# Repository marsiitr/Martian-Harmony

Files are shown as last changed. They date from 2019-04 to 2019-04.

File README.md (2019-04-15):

# Martian-Harmony
## Srishti 2019 
The idea was to build a robot that can play musical instruments in the same fashion as humans. It consists of various instruments like Flute, Keyboard, Guitar, etc. All these instruments are being played using different mechanisms.
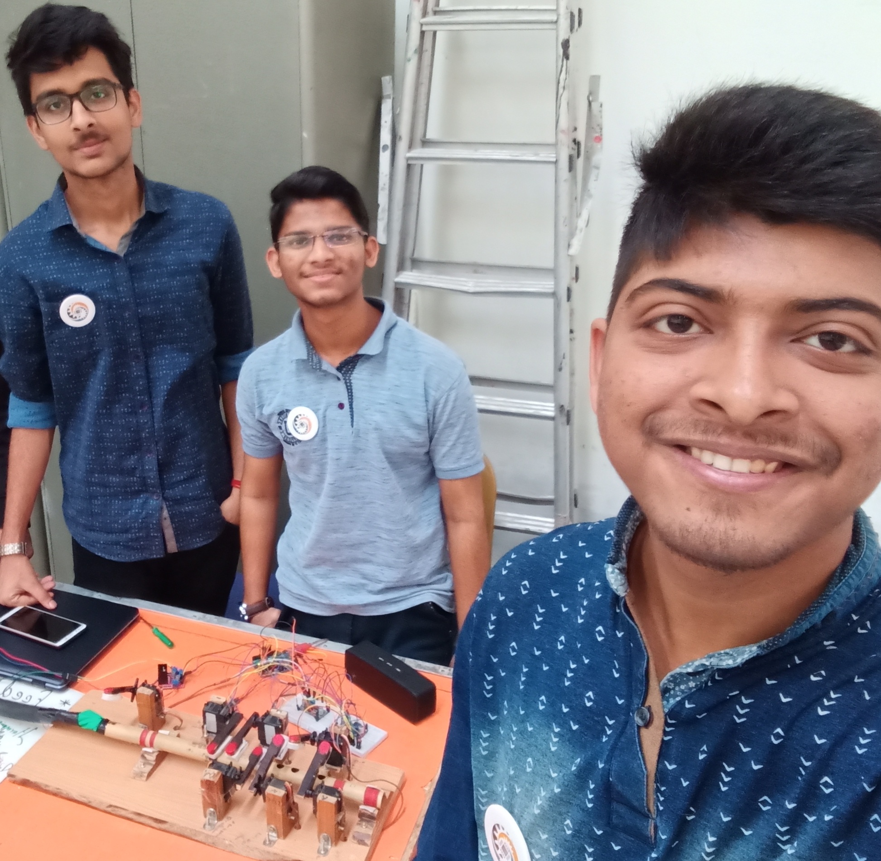
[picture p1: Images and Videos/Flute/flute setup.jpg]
Flute playing bot


To read about the working of Flute Playing Bot, click [here.](https://github.com/visvash/Martian-Harmony/blob/master/Src/Flute/README.md "Martian-Harmony Flute Playing Bot")

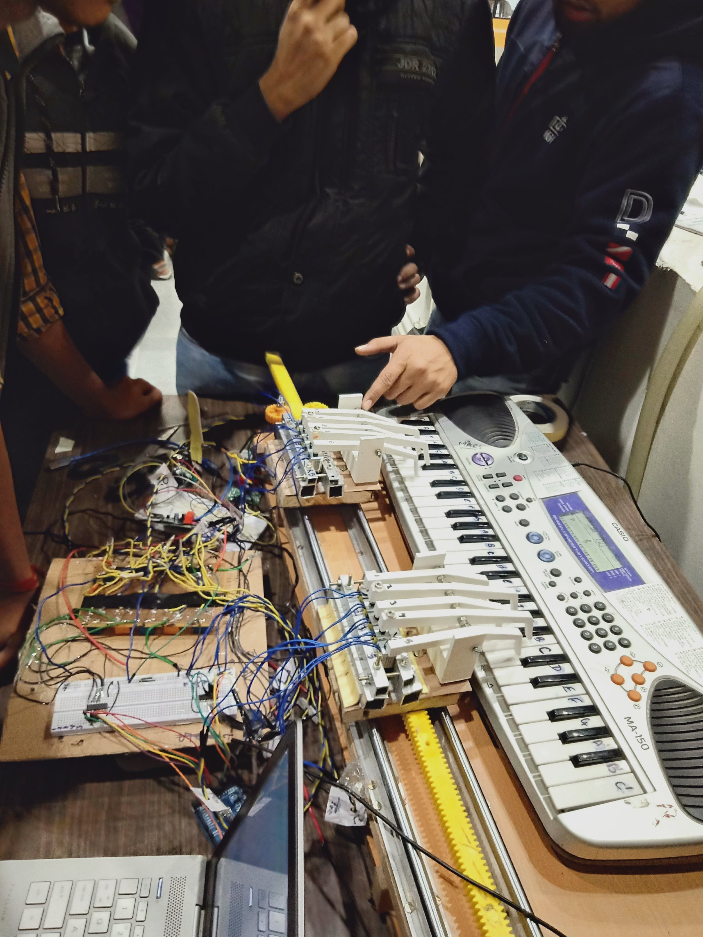
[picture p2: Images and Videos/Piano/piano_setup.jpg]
Piano playing bot


To read about working of Piano Playing Bot, click [here.](https://github.com/visvash/Martian-Harmony/blob/master/Src/Piano/README.md "Martian-Harmony Piano Playing Bot")

## Motivation:
This is a really good combination of robotics and music. There are many people who don't know how to play instruments but appreciate good music. This band could help those people live their dreams.

## Software Information Basics:
* For the mechanical model, designing of the complete setup is done on solidworks and some of the parts are 3D printed using Ultimaker 3D printer.
* We primarily needed to supply all the notes to the respective instruments and also the time at which they needed to be played. Initially we used Image processing to extract the notes using music sheet. The notes extraction was successful but we were not able to locate the time at which a note was to be played/stopped. So we dropped the idea of using a music sheet. 
* Then we used MIDI files which are basically digital music files and have the information of all the notes of different instruments and the time at which a particular note is to be played. To extract all this information from the MIDI file we used the java codes given in notes, ON/OFF and the time files.
* We did this for a few songs as only a good MIDI file was available for these much songs and for other songs either the MIDI was not available or a lot of noise was present in the MIDI file. Through MIDI files proper node times were given to the particular instruments.We have to code the instruments using arduino for those particular nodes.Check individual codes for this purpose.

## Cost structure:
### Flute:
| Item used | Quantity | Cost (INR) |
|---|---|---|
| Stepper motor |  700 x1  | 700  |
|  Servo motor  |  120 x7  | 840  |
| Arduino Mega  |  885 x1  | 885  |
|BD786Transistor| 5 x1  |  5 |
|Vacuum Cleaner | 1650 x1  | 1650 |
|12V/5A Adapter |  400 x1  | 400  |
| Heat Sink | 50 x1  |  50  |
| Jumper Wires  | 3 x45 | 135  |
| Rack & Pinion |  280 x1  | 280  |
| Nuts-Bolts 4mm|  0.5 x100|  50  |
| Screws |  0.5 x20 |  10  |
| Nails | 0.25 x20 | 5  |
|  Rubber Pipe  |  200 x1  | 200  |
| T-valve |  200 x1  | 200  |
| Miscellaneous | 350 | 150  |
| TOTAL PRICE || 5760 |

### Piano:

| Item used | Quantity | Cost (INR) |
|---|---|---|
|Solenoidal Motors| 534 x10| 5340 |
| Stepper Motor | 1345 x2  | 2690 |
| Wooden Board  |  300 x1  |  300 |
| Linear Rails  | 2750 X2  | 5500 |
| Linear Guides |  140 x4  |  560 |
| Nuts-Bolts 4mm|  0.5 x150|  75  |
| Rack & Pinion |  280 x2  |  560 |
|  Al Channels  | 50 x1  |  50  |
| Relay Switches| 20 x10 |  200 |
| Heat Sink | 50 x1  |  50  |
|12V/5A Adapter |  400 x1  | 400  |
| Arduino Mega  |  885 x1  | 885  |
| Jumper Wires  | 3 x150| 450  |
| Miscellaneous | 1500 | 1500 |
| TOTAL PRICE || 18560 |

## Applications:
We can make an automatic music band with more improvisations and additions. It could also be used for teaching puposes. It could even be used for fun purposes.

## Limitations:
* The rack and pinion mechanism used for pressure control in flute wasn't that much accurate and also added some extra noise. We could have used digital pressure controller for blowing air into the flute instead of rack and pinion mechanism. No doubt digital pressure controller would have costed more (around 2.5k inr which is about 10 times the price of rack and pinion controller used) but it would have been much more precise.
* The major difficulty that we faced in piano playing bot was the insufficient power generated by soleniodal motors. We could have used more powerful soleniodal motors for a better bot.

## Future Improvements:
We are planning to use digital pressure controller and more powerful soleniodal motors (or any better substitute) in the upcoming versions. We will be including drum kit playing bot in the next version.

## Team Members:
1. Aniket Kumar 
2. Debaditya Barman 
3. Nehal Tembhurne 
4. Rishiraj Gupta 
5. Shivansh Mathur 
6. Shukshi Raj 
7. Visvash Attri 
## Team Mentors:
1. Abhimanyu Bhambaniya 
2. Avdesh Ranwa 
3. Pradhyuman Mathur 
4. Pratikesh Thakur 
5. Sarthak Gupta

## References:
Flute Playing Bot, click [here.](https://www.youtube.com/watch?v=J8-qwAzsvn4 "youtube")
Piano Playing Bot, click [here.](https://www.youtube.com/watch?v=fmTlPdHvGRI&t=36s "youtube") 

<p align="center">
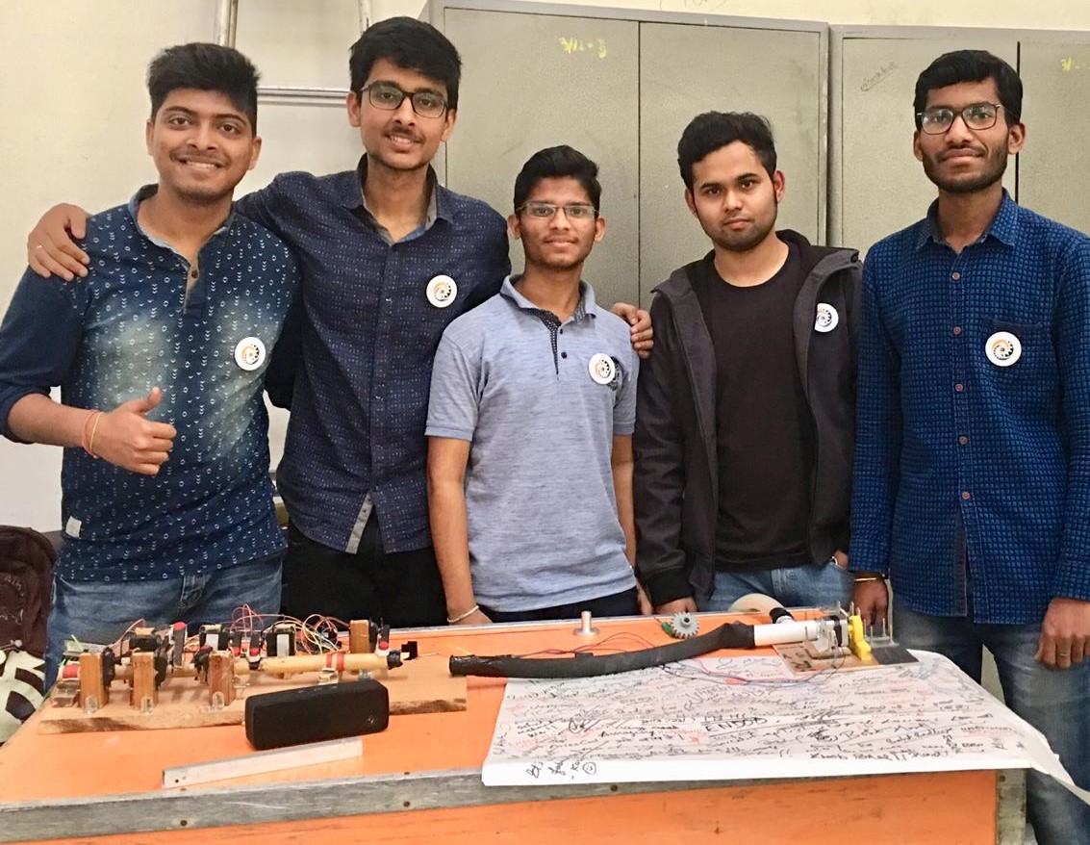
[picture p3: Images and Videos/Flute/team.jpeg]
  
  Team Martian Harmony Srishti'19
</p>

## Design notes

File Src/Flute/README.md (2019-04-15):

# Flute
Flute Playing Bot is a robot which replicates the mechanism by which a human being plays the flute. In this bot, the motion of the wooden sticks is equivalent to the motion of the fingers of human being and the pressure control which is done by the lungs in a human being while playing different chords with different frequencies is substituted by the vacuum cleaner and rack and pinion system combined.
## Pre-requisites
### Software:
1. FL-Studio:Basic knowledge of FL studio and midi file is required in order to get the information of chords and duration of playing of chords.
2. Arduino:Knowledge is required to verify working of different components as well as giving instructions for running the complete setup.
### Components used:
#### Mechanical:-
 1. 2 Wooden Boards- For setting the base for Flute and Rack and Pinion System.
 2. 1 Stand- To make a stand for Flute.
 3. 1 Rack and Pinion System- For controlling the air pressure of Vacuum Cleaner.
 4. 7 wooden sticks- They control the air from the holes of flute.
 5. 4 mm Screws
 6. Drill Machine with 4 mm Drill bit
 7. Hammer, Saw etc.
 8. A few small wooden pieces- For atttaching servo motors to the wooden block
 9. A few Nails
#### Electronics:-
 1. 7 Servo Motors (6V output)
 2. 1 Stepper Motor
 3. 1 Arduino MEGA 2560
 4. IC 786 Transistors- For converting 12V input into 6V output.
 5. Capacitors
 6. ULN 2003- For controlling Stepper Motor.
 7. 1 Vacuum Cleaner- For blowing air in the Flute System.
 8. 12 V/5A Adapter- For power supply.
 9. Heat Sink
 10. Male to Female Jumper wires - for wiring purposes.
## Importance of various components
#### 1. Servo Motors:
A servo motor is a rotary actuator or linear actuator that allows for precise control of angular or linear position, velocity and acceleration. It consists of a suitable motor coupled to a sensor for position feedback. In Flute, the servo motors are used to rotate the sticks in order to open and close the holes for different chords.
#### 2. Stepper Motor:
A stepper motor is a brushless electric DC motor that divides a full rotation into a number of equal steps. The motor's position can then be commanded to move and hold at one of these steps without any feedback sensor, as long as the motor is carefully sized to the application in respect to torque and speed. It is used to control the pressure of air coming from vacuum cleaner blown into the flute.
#### 3. Vacuum Cleaner:
It is used to blow the air into flute in controlled amount with the help of rack and pinion system and stepper motor.
#### 4. Arduino:
Arduino is an open source, computer hardware and software company, project, and user community that designs and manufactures single-board microcontrollers and microcontroller kits for building digital devices and interactive objects that can sense and control objects in the physical world.
## Design and Control
* Servo motors and stepper motors are controlled using Arduino-MEGA 2560. The information of the different chords playing for different duration as well as which holes are to be opened to produce different chords or equivalently which servo motor is to be at which angle for particular duration is feed to Arduino.
* The vacuum cleaner supplies air to the flute with the help of two pipes with one pipe going to flute and another going to rack and pinion system. The pressure control information is taken manually by varying the scale mounted on rack and pinion system and the length of the scale at different chords (the steps required by stepper motor to reach that length) is also programmed. 
* The wooden sticks with thermocol are mounted on servo motor such that the hole is completely covered. When power is supplied, the arduino, with the help of the programmed code decides the position of servo motors as well as the stepper motor for different time intervals and produces the appropriate sound at appropriate time, thus playing the tone of a song with perfection. <br/>
**Software related details can be found in Readme.md file in the parent folder.**

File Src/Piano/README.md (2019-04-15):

# Piano
Piano Playing Bot is a robot which replicates the mechanism by which a human being plays piano. In this bot 3D printed hand like structures are used to replicate the motion of human fingers over the keys of piano.Solenoid valves are used for the movement of fingers where as Stepper motors are used for motion of hand.
## Pre-requisites
### Softwares:
1. FL-Studio: Basic knowledge of FL studio and midi file is required in order to get the information of chords and duration of playing of chords.
2. Arduino: Knowledge is required to verify working of different components as well as giving instructions for running the complete setup.
### Components used:
#### Mechanical:-
 1. 1 Wooden Boards- For setting the base for Piano System.
 2. 10 Finger like 3D Printed Structures (They should contain a 4.5 mm hole at the center of them)
 3. 2 3D Printed U- shaped mounts (serves as fulcrum for see-saw mechanism of fingers)
 4. 2 15 cm threaded steel rods of diameter 4 mm each.
 5. 2 Linear Rails and 4 Linear Guides (For linear motion of hand)
 6. 2 12X12 cm Wooden Bases (for base of the hand)
 7. 4 mm nuts and bolts
 8. Drill Machine with 4 mm Drill bit
 9. Hammer, Saw, Electrical Tape, Pliers, Nails, Glue Gun, Double Side Tape etc. 
 10. 2 pairs of Rack and Pinion (atleast 15 inches long rack)
 11. Aluminium Channels (Square and L)
#### Electronics:-
 1. 2 Stepper Motors (10 KG Torque preferred).
 2. 1 Arduino MEGA 2560
 3. 10 Solenoid Valves(12 V DC each) .
 4. 2 Motor Drivers (For running Stepper Motors)
 5. 10 Relay Switches. (For ON and OFF control of Solenoids).
 6. Heat Sink
 7. ULN 2003-For controlling the voltages in Relay Switches.
 8. 12V/5A Adapter- For power supply.
 9. Breadboards and plenty of jumpers.(Male to Male, Male to Female, Female to Female)
 10. Digital Multi Meter
 11. Switches
## Importance of various components
#### 1. Stepper Motor:
A stepper motor is a brushless electric DC motor that divides a full rotation into a number of equal steps. The motor's position can then be commanded to move and hold at one of these steps without any feedback sensor, as long as the motor is carefully sized to the application in respect to torque and speed. It is used to control the pressure of air coming from vacuum cleaner blown into the flute.
#### 2. Arduino: 
Arduino is an open source, computer hardware and software company, project, and user community that designs and manufactures single-board micro-controllers and micro-controller kits for building digital devices and interactive objects that can sense and control objects in the physical world.
#### 3. Solenoid Valves: 
A solenoid valve is an electro-mechanical controlled valve. The valve features a solenoid, which is an electric coil with a movable ferromagnetic core in its center. This core is called the plunger. In rest position, the plunger closes off a small orifice. An electric current through the coil creates a magnetic field. The magnetic field exerts a force on the plunger. As a result, the plunger is pulled toward the center of the coil so that the orifice opens. This is the basic principle that is used to open and close solenoid valves.
#### 4. Relay Switches: 
Relays are switches that open and close circuits electro-mechanically or electronically. Relays control one electrical circuit by opening and closing contacts in another circuit. As relay diagrams show, when a relay contact is normally open (NO), there is an open contact when the relay is not energized. When a relay contact is Normally Closed (NC), there is a closed contact when the relay is not energized. In either case, applying electrical current to the contacts will change their state.
#### 5. Motor Drivers: 
A motor driver is a little current amplifier; the function of motor drivers is to take a low-current control signal and then turn it into a higher-current signal that can drive a motor.
## Design and Control
* First of all mount keyboard on the big wooden board, so that it does not get displaced from its position. Take the measurements of keys and wooden base (mount the U-shaped stand perpendicular to its surface along its one edge) such that it can cover 5 consecutive keys.
* Mount the fingers of the hand as WBWBW where W stands for shorter finger for white keys and B stands for longer finger for black keys. Mounting is done with the help of threaded rod that mates through holes in the clamp, 5 fingers and optimum number of nuts. 
* Now place all keys at an appropriate distance from each other, such that they cover one key each (You can use Tape to create distance or something which doesn't allow them to move from their place, but make sure they are free to rotate). Fix this entire structure on a linear rails fixed parallel on wooden board with the help of linear guides such that it is able to slide along the rails. 
* Stick all the solenoids on the back of the hand base exactly under the fingered structures (with the help of aluminium channels) such that when current is passed through them, they push the fingers and the key is pressed (See-saw mechanism). Attach the pinions to the shafts of Stepper Motors. 
* Attach the rack to the movable part of hands. Mount each stepper on either side of the keyboard and mount the slider using wooden blocks such that the rack and pinion work smoothly and all the keys are pressed properly.
* Make the circuits using relays and ULN such that each relay controls a solenoid. Connect all solenoids to relay so that relay work as a switch.Use motor drivers to drive the steppers.Male all connections to Arduino Mega. Power the circuits using 12V/5A adapters. Upload the files to Arduino and you are ready to rock.

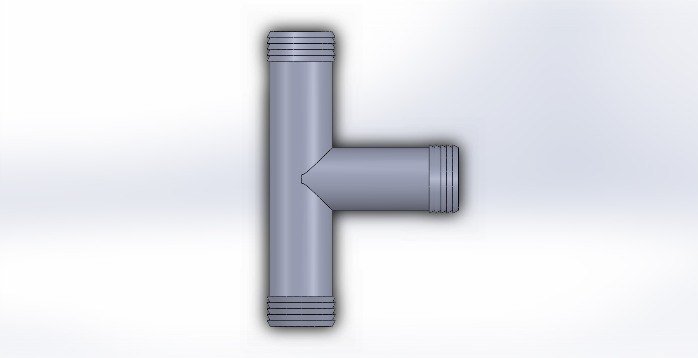
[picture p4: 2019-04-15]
Mechanical Design/Flute/valve_for_pressure_control.JPG

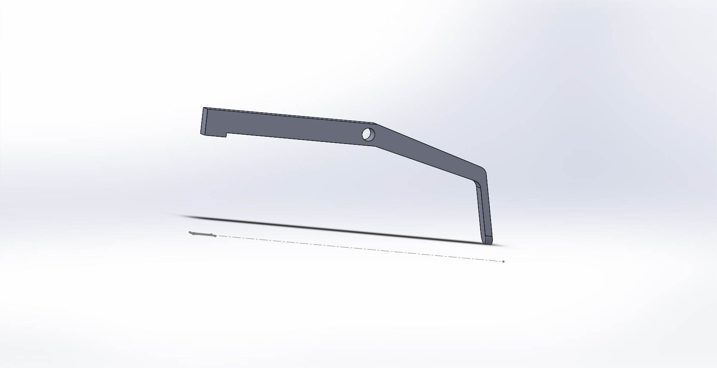
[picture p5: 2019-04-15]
Mechanical Design/Piano/shorter_claw_white.JPG

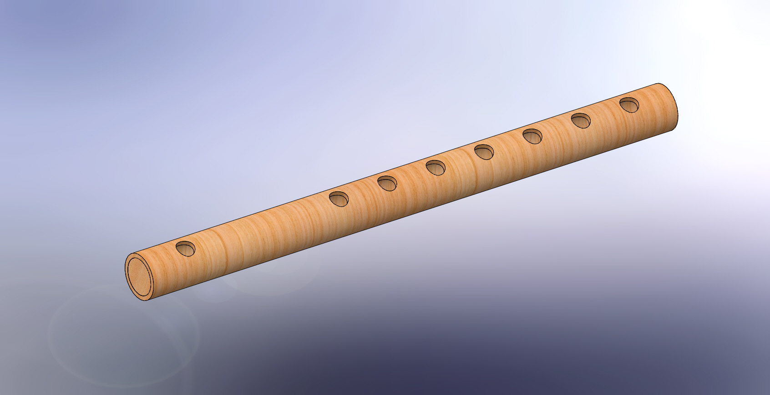
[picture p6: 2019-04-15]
Mechanical Design/Flute/Flute.JPG

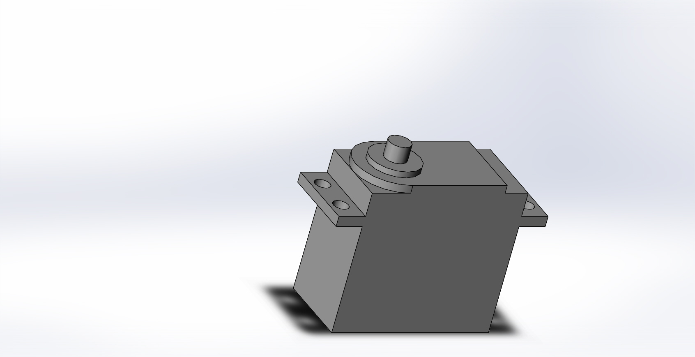
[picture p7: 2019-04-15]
Mechanical Design/Flute/servo large for flute.JPG

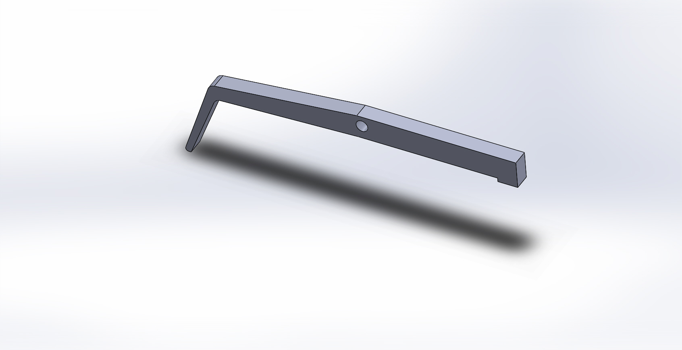
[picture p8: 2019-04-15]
Mechanical Design/Piano/longer_claw_black.JPG

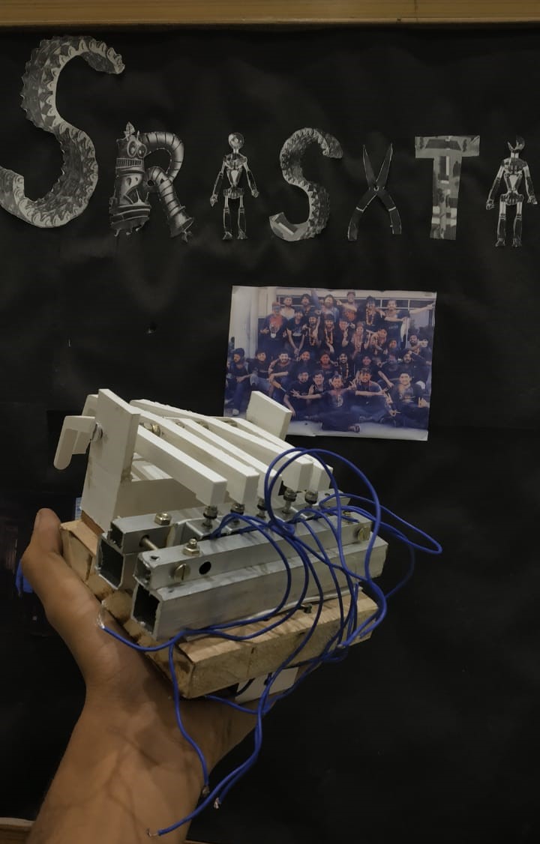
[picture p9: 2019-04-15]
Images and Videos/Piano/hand.jpeg

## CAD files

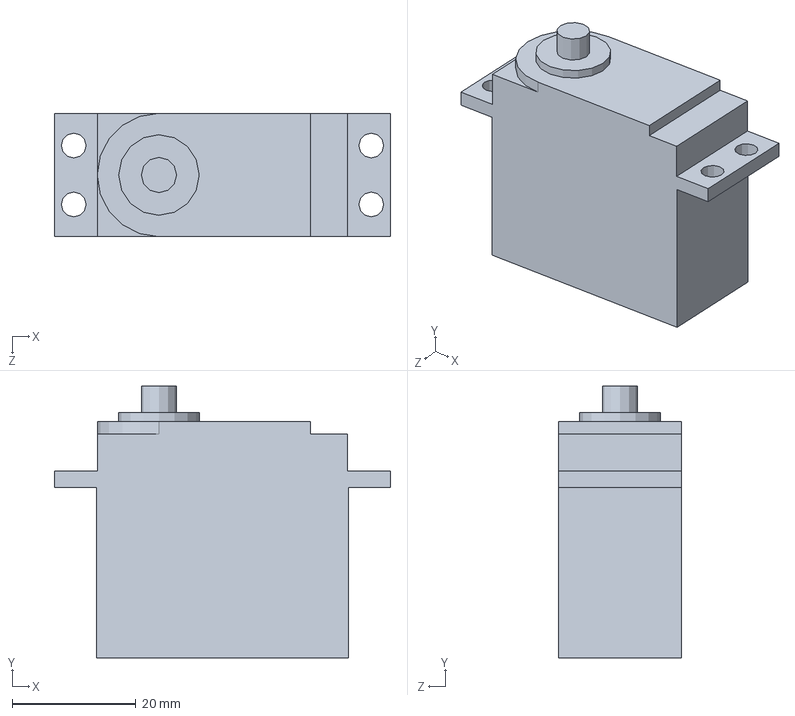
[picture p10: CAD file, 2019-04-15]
Mechanical Design/Flute/servo large for flute.SLDPRT
54.2 x 43.8 x 19.9 mm

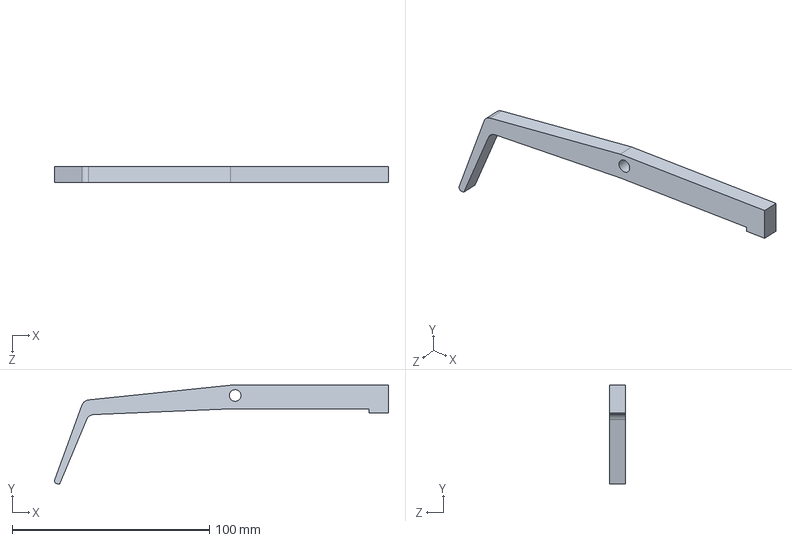
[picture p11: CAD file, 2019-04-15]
Mechanical Design/Piano/longer_claw_black.SLDPRT
169.3 x 50.0 x 8.00 mm

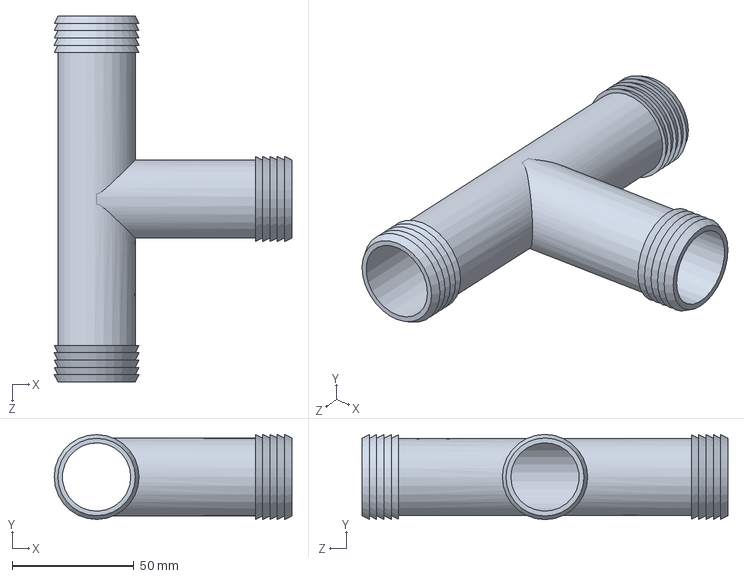
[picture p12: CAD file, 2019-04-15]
Mechanical Design/Flute/valve_for_pressure_control.SLDPRT
97.4 x 34.9 x 150.0 mm

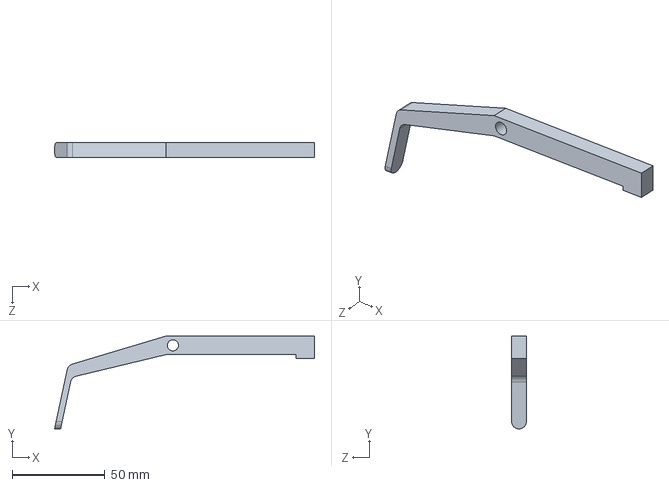
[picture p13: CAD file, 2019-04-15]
Mechanical Design/Piano/shorter_claw_white.SLDPRT
140.0 x 50.0 x 8.00 mm

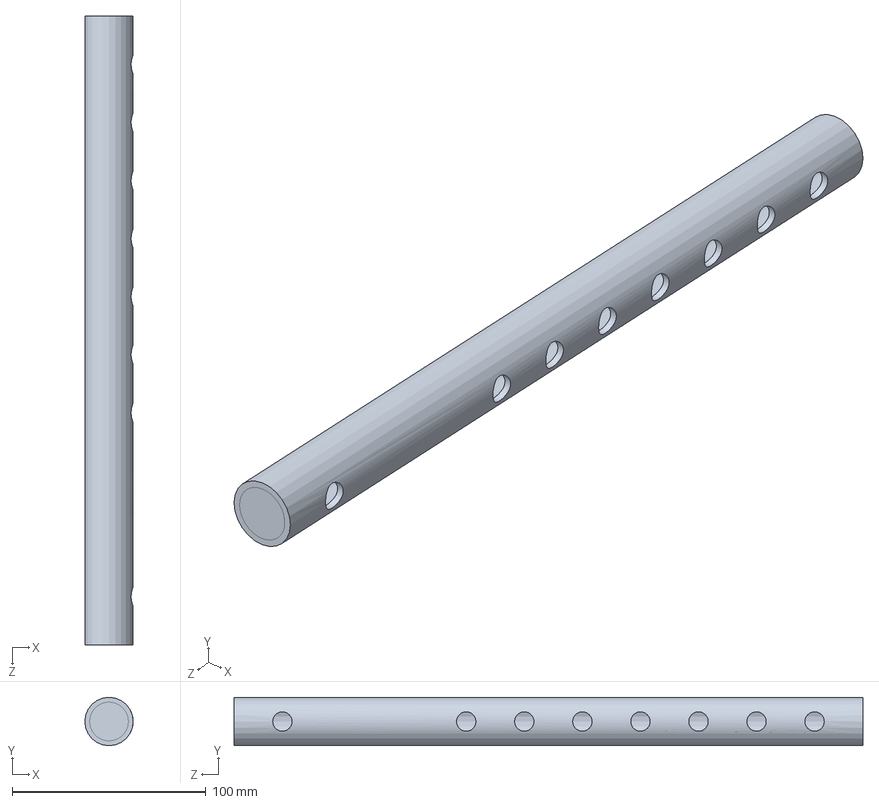
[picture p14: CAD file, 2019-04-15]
Mechanical Design/Flute/FLute.SLDPRT
25.0 x 25.0 x 325.0 mm

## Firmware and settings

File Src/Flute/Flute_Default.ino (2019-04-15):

#include <Servo.h>
#include <Stepper.h>
#define SIZE 200
#define OPEN 0
#define HALF 1
#define FULL 2

#define STEPSPR 150

Servo myservo1,myservo2,myservo3,myservo4,myservo5,myservo6,myservo7;  // create servo objects to control a servo. Twelve servo objects can be created on most boards

Stepper stepper(STEPSPR, A0,A1,A2,A3 );
int pos=0;
int posInit1=45,posInit2=45,posInit3=45,posInit4=45,posInit5=45,posInit6=45;   // variable to store the servo initial positions
int stepInit=0;                                         
boolean offFlag = false;
int stepC=19,stepC_High=37,stepD=12,stepD_High=9,stepE=5,stepE_High=28,stepF=10,stepF_High=8,stepG=14,stepG_sharp=0,stepA=17,stepA_High=23,stepB=24;//stepB=24,stepC=19
int Open1=30,Open2=0,Open3=0,Open4=30,Open5=0,Open6=30;
int Half1=40,Half2=40,Half3=40,Half4=40,Half5=40,Half6=40;
int Full1=0,Full2=30,Full3=30,Full4=0,Full5=30,Full6=0;
int prevFlag1=0,prevFlag2=0,prevFlag3=0,prevFlag4=0,prevFlag5=0,prevFlag6=0; 
int currFlag1=0,currFlag2=0,currFlag3=0,currFlag4=0,currFlag5=0,currFlag6=0;
int iFlute=0;

int t1,t2;
//flag = 0 for open
//flag = 1 for close
//Data for kal ho na ho
char noteFlute[SIZE]={'C','B','C','B','C','B','C','E','D','C','B','A','B','A','B','C','B','C','B','C','B','C','E','D','C','B','A','B','A','B','B','G','A','C','A','F','G','A','G','G','A','C','A','G','F','F','A','A','G'};
int timeFlute[SIZE]={0,642,857,1500,1714,2357,2571,2785,3000,3214,3428,4071,4285,4928,5142,6857,7500,7714,8357,8571,9214,9428,9643,9857,10071,10285,10928,11142,11785,12000,13714,14571,15000,15428,15642,18000,18428,18857,19072,21428,21857,22285,22500,24214,24428,24857,25285,25714,25928};
byte onOffFlute[SIZE]={1,1,1,1,1,1,1,1,1,1,1,1,1,1,1,1,1,1,1,1,1,1,1,1,1,1,1,1,1,1,0,1,1,1,1,1,1,1,1,1,1,1,1,1,1,1,1,1,1};

//Data for harry potter
//char noteFlute[SIZE]={'B','E','G','F','E','B','A','F','E','G','F','D','F','B','B','E','G','F','E','B','D','C','C','G','C','B','A','F','G','E','G','B','G','B','G','C','B','A','F','G','B','A','A','B','B','G','B','G','B','G','D','C','C','G','C','B','A','F','G','E'};
//int timeFlute[SIZE]={1500,1800,2250,2400,2700,3300,3600,4500,5400,5850,6000,6300,6900,7200,8700,9000,9450,9600,9900,10500,10800,11400,11700,12300,12600,13050,13200,13500,14100,14400,15900,16200,16800,17100,17700,18000,18600,18900,19500,19800,20250,20400,20700,21300,21600,23100,23400,24000,24300,24900,25200,25800,26100,26700,27000,27450,27600,27900,28500,28800};
//byte onOffFlute[SIZE]={1,1,1,1,1,1,1,1,1,1,1,1,1,1,1,1,1,1,1,1,1,1,1,1,1,1,1,1,1,1,1,1,1,1,1,1,1,1,1,1,1,1,1,1,1,1,1,1,1,1,1,1,1,1,1,1,1,1,1,1};

//data for baazigar
//char noteFlute[SIZE]={'D','D','C','D','A','D','D','D','C','D','A','D','D','C','D','A','D','D','D','C','D','A','D','D','C','D','A','D','D','D','C','D','A','D','D','C','D','A','D','D','D','C','D','A','D','D','C','D','A','D','D','D','C','D','A','D','D','C','D','A','D','D','D','C','D','A'};
//int timeFlute[SIZE]={1920,2640,2880,3120,3360,3840,4200,4560,4800,5040,5280,5760,6480,6720,6960,7200,7680,8040,8400,8640,8880,9120,9600,10320,10560,10800,11040,11520,11880,12240,12480,12720,12960,13440,14160,14400,14640,14880,15360,15720,16080,16320,16560,16800,17280,18000,18240,18480,18720,19200,19560,19920,20160,20400,20640,21120,21840,22080,22320,22560,23040,23400,23760,24000,24240,24480};
//byte onOffFlute[SIZE]={1,1,1,1,1,1,1,1,1,1,1,1,1,1,1,1,1,1,1,1,1,1,1,1,1,1,1,1,1,1,1,1,1,1,1,1,1,1,1,1,1,1,1,1,1,1,1,1,1,1,1,1,1,1,1,1,1,1,1,1,1,1,1,1,1,1};

//Data for ek ladki ko dekha
//char noteFlute[SIZE]={'G','C','C','B','C','D','B','C','D','B','C','D','B','C','C','D','B','C','D','B','B','C','D','D','B','C','D','B','C','C','C','C','B','C','C','G','B','A','B','C','C','B','G','B','A','B','C','C','B','G','B','A','A','A','A','G','G','E','F','A','G','G','G','G','F','F','E','F','A','G','G','G','A','A','F','A','C','A','G','G','G','G','G','B','C','E','D','D','D','B','B','G','B','C','E','D','C','D','D','B','C','D','B','C','D','B','C','E','B','C','C','G','B','C','D','C','G','B','C','D','C','G','C','C','C','G','A','E','F','A','G','G','B','C','D','C','G','B','C','D','C','G','C','C','C','G','A','E','F','A','G'};
//int timeFlute[SIZE]={0,8571,11125,11526,11964,12625,13241,13669,14334,14995,15370,16062,16250,16700,17120,21450,21861,22267,22964,23584,23959,24607,24674,25303,25620,25691,26370,26441,26973,27428,28316,28683,28928,29580,29843,30071,30285,30651,30879,31803,32089,32625,33017,33718,34080,34321,35227,35571,35959,36428,37098,37473,37709,38464,38575,38674,39392,39504,39852,40165,40513,40816,41107,41843,42004,42839,42892,43303,43665,43915,44303,44589,45410,45812,46120,46781,46973,47383,47785,47991,48687,48892,49285,50142,50464,50785,51174,51424,52330,52714,53165,53250,53589,53870,54241,54558,54857,60040,63049,63392,63468,64071,64660,65133,65816,66433,66830,67495,67696,68200,68647,70482,81000,81424,81803,81901,82285,84428,84852,85232,85330,85714,87857,88281,88583,88660,88758,89142,91285,91709,92089,92571,94714,95138,95517,95616,96000,98142,98566,98946,99044,99428,101571,101995,102271,102375,102473,102857,105000,105424,105803,106285};
//byte onOffFlute[SIZE]={0,1,1,1,1,1,1,1,1,1,1,1,1,1,1,1,1,1,1,1,1,0,1,1,0,1,1,1,1,1,1,1,0,1,1,0,1,1,1,1,1,0,1,1,1,1,1,1,0,1,1,1,1,1,0,1,1,0,1,1,1,1,1,1,1,1,0,1,1,1,1,1,1,1,0,1,1,1,1,1,1,1,1,1,1,1,1,1,1,1,1,0,1,1,1,1,1,1,1,0,1,1,1,1,1,1,1,1,1,1,1,0,1,1,1,1,1,1,1,1,1,1,1,1,0,1,1,1,1,1,1,1,1,1,1,1,1,1,1,1,1,1,1,1,0,1,1,1,1,1,1,1};

//Data for vande mataram
//char noteFlute[SIZE]={'C','D','F','G','F','G','F','G','B','C','B','C','C','C','D','A','B','A','G','G','G','A','F','E','D','D','D','D','D','G','F','E','D','E','D','C','C','C','D','F','G','F','G','G','G','B','A','A','A','G','F','G','B','C','B','C','F','G','B','B','B','B','B','B','B','C','B','C','B','C','B','B','B','B','B','C','B','C','B','C','D','C','B','A','B','A','A','A','G','D','D','D','F','F','F','E','D','D','D','D','D','A','B','A','G','A','G','F','G','B','B','B','B','B','B','B','B','B','C','B','C','F','G','B','C','B','C','F','G','B','C','B','C','G'};
//int timeFlute[SIZE]={0,666,1666,2000,2333,2666,5333,6000,7000,7333,7666,8000,10616,10666,11000,11340,11833,12333,12666,13283,13333,13666,14006,15000,15333,15950,16000,16283,16333,16666,17000,17333,18000,18333,18666,19000,21283,21333,22000,22333,22666,23000,23333,24283,24333,24666,25000,25283,25333,25666,26666,27333,28333,28666,29000,29333,32000,32666,33333,33950,34000,34616,34666,34950,35000,35333,35666,36000,37000,37333,38666,39283,39333,39616,39666,40000,40333,40666,41333,41666,42000,42333,42666,43000,43333,43666,43950,44000,44333,45333,45616,45666,46000,46283,46333,46666,47000,47950,48000,48283,48333,48666,49006,49333,49666,50333,50666,52000,52333,52666,53283,53333,53616,53666,53950,54000,54950,55000,55333,55666,56000,57333,58000,59000,59333,59666,60000,62666,63333,64333,64666,65000,65333,65500};
//byte onOffFlute[SIZE]={1,1,1,1,1,1,1,1,1,1,1,1,0,1,1,1,1,1,1,0,1,1,1,1,1,0,1,0,1,1,1,1,1,1,1,1,0,1,1,1,1,1,1,0,1,1,1,0,1,1,1,1,1,1,1,1,1,1,1,0,1,0,1,0,1,1,1,1,1,1,1,0,1,0,1,1,1,1,1,1,1,1,1,1,1,1,0,1,1,1,0,1,1,0,1,1,1,0,1,0,1,1,1,1,1,1,1,1,1,1,0,1,0,1,0,1,0,1,1,1,1,1,1,1,1,1,1,1,1,1,1,1,1,O};

//Data For Are re re ye kya hua song :P
//char noteFlute[SIZE]={'A','B','C','A','E','D','C','B','A','B','C','A','F','E','A','B','C','A','E','D','C','B','C','D','E','B','C','B','A','G'};
//int timeFlute[SIZE]={5615,5824,6032,6263,6699,7166,7870,8050,9203,9435,9638,9842,10287,10708,12745,12953,13166,13388,13828,14287,14953,15162,16032,16287,16439,16685,16888,17379,17800,17900};
//byte onOffFlute[SIZE]={1,1,1,1,1,1,1,1,1,1,1,1,1,1,1,1,1,1,1,1,1,1,1,1,1,1,1,1,1,0};

//Data for raghupati raghav
//char noteFlute[SIZE]={'D','D','D','G','G','G','G','F','G','A','G','F','E','F','A','A','A','C','B','C','A','A','A','G','A','G','F','E','F','A','G','G','G','B','B','B','B','B','A','G','A','C','C','C','B','C','A','A','A','C','C','C','D','D','D','C','A','A','G'};
//int timeFlute[SIZE]={72,190,552,796,1036,1194,1516,1996,2232,2472,2712,2956,3436,3916,4872,5570,5832,6316,6796,7276,7752,8236,9196,9672,10152,10392,10632,11116,11596,12552,13032,13226,13516,15432,16074,16396,17098,17356,18316,18796,19272,19756,19974,20232,20712,21196,23116,23350,23592,24076,24438,24556,25036,25996,26476,26956,27916,28392,28876};
//byte onOffFlute[SIZE]={1,0,1,1,1,0,1,1,1,1,1,1,1,1,1,0,1,1,1,1,1,1,1,1,1,1,1,1,1,1,1,0,1,1,0,1,0,1,1,1,1,1,0,1,1,1,1,0,1,1,0,1,1,1,1,1,1,1,1};

void setup() {
  Serial.begin(9600);
  myservo1.attach(8);
  myservo2.attach(9);
  myservo3.attach(7);
  myservo4.attach(6);
  myservo5.attach(5);
  myservo6.attach(12);
  myservo7.attach(11);
  stepper.setSpeed(200);
  myservo1.write(45);
  myservo2.write(45);
  myservo3.write(45);
  myservo4.write(45);
  myservo5.write(45);
  myservo6.write(45);
  myservo7.write(5);
  t1=millis();
  
}

void loop() 
{
  if(1){
    t1=millis();
    while(1){
      t2=millis();
      Serial.println(t1);
      Serial.println(t2);
      if (abs((t2-t1) - timeFlute[iFlute])<140) fluteCall(); 
      //if (abs((t2-t1) - timeFlute[iFlute])<=0) fluteCall(); 
      else if((t2-t1)>timeFlute[iFlute]) {
        //iFlute++;
        Serial.print("Timer Flute Overflow : ");
        Serial.println(t2-t1); 
      }
    }
  }
  else Serial.println("pinOff");
}

void C(){
pressure(stepInit,stepC);
  currFlag1 = 1;//close
  currFlag2 = 1;
  currFlag3 = 1;
  currFlag4 = 0;
  currFlag5 = 0;//open
  currFlag6 = 0;
  newNote();
  posInit1=45;
  posInit2=45;
  posInit3=45;
  posInit4=75;
  posInit5=15;
  posInit6=75;
}

void C_High(){
  pressure(stepInit,stepC_High);
  currFlag1 = 1;
  currFlag2 = 1;
  currFlag3 = 1;
  currFlag4 = 0;
  currFlag5 = 0;
  currFlag6 = 0;
  newNote();
  posInit1=3;
  posInit2=63;
  posInit3=63;
  posInit4=32;
  posInit5=32;
  posInit6=32;
}

void D(){
  pressure(stepInit,stepD);
  currFlag1 = 1;
  currFlag2 = 1;
  currFlag3 = 1;
  currFlag4 = 0;
  currFlag5 = 0;
  currFlag6 = 0;
  newNote();
  posInit1=45;
  posInit2=45;
  posInit3=45;
  posInit4=75;
  posInit5=15;
  posInit6=75;
}

void D_High(){
  pressure(stepInit,stepD_High);
  currFlag1 = 1;
  currFlag2 = 1;
  currFlag3 = 0;
  currFlag4 = 0;
  currFlag5 = 0;
  currFlag6 = 0;
  newNote();
  posInit1=3;
  posInit2=63;
  posInit3=39;
  posInit4=32;
  posInit5=32;
  posInit6=32;
}

void E(){
  pressure(stepInit,stepE);
  currFlag1 = 1;
  currFlag2 = 0;
  currFlag3 = 0;
  currFlag4 = 0;
  currFlag5 = 0;
  currFlag6 = 0;
  newNote();
  posInit1=45;
  posInit2=15;
  posInit3=15;
  posInit4=75;
  posInit5=15;
  posInit6=75;
}

void F_note(){
  pressure(stepInit,stepF);
  currFlag1 = 0;
  currFlag2 = 0;
  currFlag3 = 0;
  currFlag4 = 0;
  currFlag5 = 0;
  currFlag6 = 0;
  newNote();
  posInit1=75;
  posInit2=15;
  posInit3=15;
  posInit4=75;
  posInit5=15;
  posInit6=75;
}

void F_High(){
  pressure(stepInit,stepF_High);
  currFlag1 = 0;
  currFlag2 = 0;
  currFlag3 = 0;
  currFlag4 = 0;
  currFlag5 = 0;
  currFlag6 = 0;
  newNote();
  posInit1=32;
  posInit2=39;
  posInit3=39;
  posInit4=32;
  posInit5=32;
  posInit6=32;}

void G(){
  pressure(stepInit,stepG);
  currFlag1 = 1;
  currFlag2 = 1;
  currFlag3 = 1;
  currFlag4 = 0;
  currFlag5 = 0;
  currFlag6 = 0;
  newNote();
  posInit1=45;
  posInit2=45;
  posInit3=45;
  posInit4=75;
  posInit5=15;
  posInit6=75;}

void G_High(){
  pressure(stepInit,stepG_sharp);
  currFlag1 = 1;
  currFlag2 = 1;
  currFlag3 = 1;
  currFlag4 = 1;
  currFlag5 = 1;
  currFlag6 = 1;
  newNote();
  posInit1=3;
  posInit2=63;
  posInit3=63;
  posInit4=3;
  posInit5=3;
  posInit6=3;}

void A(){
  pressure(stepInit,stepA);
  currFlag1 = 0;
  currFlag2 = 1;
  currFlag3 = 0;
  currFlag4 = 0;
  currFlag5 = 0;
  currFlag6 = 0;
  newNote();
  posInit1=75;
  posInit2=45;
  posInit3=15;
  posInit4=75;
  posInit5=15;
  posInit6=75;
}

void A_High(){
  pressure(stepInit,stepA_High);
 
  currFlag1 = 1;
  currFlag2 = 1;
  currFlag3 = 1;
  currFlag4 = 1;
  currFlag5 = 1;
  currFlag6 = 0;
  newNote();
  posInit1=3;
  posInit2=63;
  posInit3=63;
  posInit4=3;
  posInit5=3;
  posInit6=32;
}

void B(){
  pressure(stepInit,stepB);
  currFlag1 = 1;
  currFlag2 = 1;
  currFlag3 = 1;
  currFlag4 = 1;
  currFlag5 = 1;
  currFlag6 = 1;
  newNote();
  posInit1=45;
  posInit2=45;
  posInit3=45;
  posInit4=45;
  posInit5=45;
  posInit6=45;
}


void fluteCall(){
  Serial.print("Timer : ");
  Serial.print(t2-t1);
  Serial.print(" Flute : ");
  Serial.print(timeFlute[iFlute]);
  Serial.print("  "); //Serial.println(noteFlute[iFlute]);
  //Serial.print(flute);
  //Serial.print("  ");  
  if(onOffFlute[iFlute]==0) {
        if(offFlag==false){
              for (pos = 5; pos <=35 ; pos += 1) 
              { 
                myservo7.write(pos);
                delay(10);
                offFlag = true;
              }
            }
            Serial.println(noteFlute[iFlute]);
    iFlute++;
  }
  else if(onOffFlute[iFlute]==1){
      switch(noteFlute[iFlute]){
      case 'A':
            if(offFlag==true){
              for (pos = 35; pos >=5 ; pos -= 1) 
              { 
                myservo7.write(pos);
                delay(10);
              }
              offFlag = false;
            }
            Serial.println(noteFlute[iFlute]);
            A();
            break;
      case 'B':
            if(offFlag==true){
              for (pos = 35; pos >=5 ; pos -= 1) 
              { 
                myservo7.write(pos);
                delay(10);
              }
              offFlag = false;
            }
            Serial.println(noteFlute[iFlute]);
            B();
        break;
      case 'C':
            if(offFlag==true){
              for (pos = 35; pos >=5 ; pos -= 1) 
              { 
                myservo7.write(pos);
                delay(10);
              }
              offFlag = false;
            }
            Serial.println(noteFlute[iFlute]);
            C();
        break;
     case 'D':
            if(offFlag==true){
              for (pos = 35; pos >=5 ; pos -= 1) 
              { 
                myservo7.write(pos);
                delay(10);
              }
              offFlag = false;
            }
            Serial.println(noteFlute[iFlute]);
            D();
            break;
     case 'E':
            if(offFlag==true){
              for (pos = 35; pos >=5 ; pos -= 1) 
              { 
                myservo7.write(pos);
                delay(10);
              }
              offFlag = false;
            }
            Serial.println(noteFlute[iFlute]);
            E();
        break;
     case 'F':
            if(offFlag==true){
              for (pos = 35; pos >=5 ; pos -= 1) 
              { 
                myservo7.write(pos);
                delay(10);
              }
              offFlag = false;
            }
            Serial.println(noteFlute[iFlute]);
            F_note();
        break;
     case 'G':
            if(offFlag==true){
              for (pos = 30; pos >=0 ; pos -= 1) 
              { 
                myservo7.write(pos);
                delay(10);
              }
              offFlag = false;
            }
            Serial.println(noteFlute[iFlute]);
            G();
        break;
      default:
             if(offFlag==false){
            for (pos = 5; pos <=35 ; pos += 1) 
            { 
              myservo7.write(pos);
              delay(10);
              offFlag = true;
            }
         }
    }
    iFlute++;
  }
  return;
}
void pressure(int &stepInit, int stepFinal)
{
  stepper.step(stepInit - stepFinal);  
  stepInit = stepFinal;
 }
void newNote(){
  for(int i=0;i<=30;i++)
  {
    if (prevFlag1>currFlag1) myservo1.write(posInit1+i);
      else if(prevFlag1<currFlag1) myservo1.write(posInit1-i);
    if (prevFlag2>currFlag2) myservo2.write(posInit2-i);
      else if(prevFlag2<currFlag2) myservo2.write(posInit2+i);
    if (prevFlag3>currFlag3) myservo3.write(posInit3-i);
      else if(prevFlag3<currFlag3) myservo3.write(posInit3+i);
    if (prevFlag4>currFlag4) myservo4.write(posInit4+i);
      else if(prevFlag4<currFlag4) myservo4.write(posInit4-i);
    if (prevFlag5>currFlag5) myservo5.write(posInit5-i);
      else if(prevFlag5<currFlag5) myservo5.write(posInit5+i);
    if (prevFlag6>currFlag6) myservo6.write(posInit6+i);
      else if(prevFlag6<currFlag6) myservo6.write(posInit6-i);  
      
        delay(5);
  }
  prevFlag1=currFlag1;
  prevFlag2=currFlag2;
  prevFlag3=currFlag3;
  prevFlag4=currFlag4;
  prevFlag5=currFlag5;
  prevFlag6=currFlag6;
}

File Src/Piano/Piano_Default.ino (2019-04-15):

#include<Stepper.h>
#define SIZE 200  // array size
#define STEPPOS 300// max steps
int stepInitR = 0; // stepper initial position .
int solenoidPin6 = 35, solenoidPin7 = 32  , solenoidPin8 = 31 ,   solenoidPin9 =  33 ,  solenoidPin10 = 34;
int stepPerKeyR = 54; //57 // As the Name specifys how many steps should be taken to reach the very next key.


//Data For Are re re ye kya hua song :P
char notePianoR[SIZE] = {'A', 'B', 'c', 'A', 'e', 'd', 'c', 'B', 'A', 'B', 'c', 'A', 'f', 'e', 'A', 'B', 'c', 'A', 'e', 'd', 'c', 'B', 'c', 'd', 'e', 'B', 'c', 'B', 'A', 'X'}; // Note array
int timePianoR[SIZE] = {5615, 5615, 5824, 6032, 6263, 6699, 7166, 7870, 8050, 9203, 9435, 9638, 9842, 10287, 10708, 12745, 12953, 13166, 13388, 13828, 14287, 14953, 15162, 16032, 16287, 16439, 16685, 16888, 17379, 17800, 18000}; // time array
//char notePianoR[SIZE]={'


int step_CR = 3, step_DR = 2, step_ER = 1, step_GR = -1, step_AR = 9, step_BR = 8, step_FR = 0, step_cmajor=0,step_bmajor=1, step_amojor=2; //int step_CR=0,step_DR=0,step_ER=2,step_FR=2,step_GR=2,step_AR=5,step_BR=5,stepC_mazor=00;
int step_cR = 10, step_dR = 9, step_eR = 10, step_fR = 9, step_gR = 6, step_aR = 12, step_bR = 11; //int step_cR=5,step_dR=5,step_eR=5,step_fR=6,step_gR=7,step_aR=9,step_bR=9;//int step_CR = 3, step_DR = 2, step_ER = 1, step_GR = -1, step_AR = 5, step_BR = 4, step_FR = 0, step_cmajor=0,step_bmajor=1, step_amojor=2; //int step_CR=0,step_DR=0,step_ER=2,step_FR=2,step_GR=2,step_AR=5,step_BR=5,stepC_mazor=00;
//int step_cR = 10, step_dR = 9, step_eR = 8, step_fR = 7, step_gR = 6, step_aR = 12, step_bR = 11; //int step_cR=5,step_dR=5,step_eR=5,step_fR=6,step_gR=7,step_aR=9,step_bR=9;


int Y = sizeof(notePianoR);
int iPianoR = 0;
// initializing steppers
Stepper stepperR(STEPPOS, 11, 7);
Stepper stepperL(STEPPOS, 9,10);
int prevFlag6 = 0, prevFlag7 = 0, prevFlag8 = 0, prevFlag9 = 0, prevFlag10 = 0;
int currFlag6 = 0, currFlag7 = 0, currFlag8 = 0, currFlag9 = 0, currFlag10 = 0;
//int iPiano=0;
int t1, t2;
//flag = 0  for open
//flag = 1 for close
void setup() {
  // put your setup code here, to run once:
  Serial.begin(9600);
  // 5 solenoid in one hand , connected as output pins.
  stepperR.setSpeed(80);// stepper speed is set to 100.

  pinMode(solenoidPin6, OUTPUT);
  pinMode(solenoidPin7, OUTPUT);
  pinMode(solenoidPin8, OUTPUT);
  pinMode(solenoidPin9, OUTPUT);
  pinMode(solenoidPin10, OUTPUT);
  pinMode(A0, OUTPUT);
  pinMode(A1, OUTPUT);
  pinMode(A2, OUTPUT);
  pinMode(A3,OUTPUT);


  //digitalWrite(A0,HIGH);// Stepper R
  //digitalWrite(A1,HIGH);
}

void loop() {
  
  for(int i=0;i<Y;i++) {

  callPianoR();
    Serial.println(stepInitR);
   
  
   
   delay(timePianoR[iPianoR+1]-timePianoR[iPianoR]); // for how much time the key has to be pressed 
  Serial.println(timePianoR[iPianoR+1]-timePianoR[iPianoR]); 
      }
       
//AR_1();
//delay(1000);
//
//BR_1();
//while(1);
  //digitalWrite(A0,HIGH);// Stepper R
  //digitalWrite(A1,HIGH);
  //   int x=stepFinalR;
  // stepperR.step(stepPerKeyR*(stepInitR-x));

  //  digitalWrite(A0,HIGH);// Stepper R
  //  digitalWrite(A1,HIGH);
  //  stepperR.step(40);
  //    delay(300);
  //  digitalWrite(A0,LOW);// Stepper R
  //  digitalWrite(A1,LOW);
  //  digitalWrite(A0,HIGH);// Stepper R
  //  digitalWrite(A1,HIGH);
  //  stepperR.step(-40);
  //  delay(300);
  //  digitalWrite(A0,LOW);// Stepper R
  //  digitalWrite(A1,LOW);
}
/* callPianoR is a function which will check which note is to be pressed . and accordingly  note is called . At the end of notearray there is a note named 'X'
  which is made to bring the stepper to it's initial position after the execution of complete code.*/
void callPianoR()
{

  switch (notePianoR[iPianoR]) // FOR right hand
  {
    //  case '0' :      zero(); break;
    case 'A' :      AR_1(); break;
    case 'B' :      BR_1(); break;
    case 'C' :      CR_1(); break;
    case 'D' :      DR_1(); break;
    case 'E' :      ER_1(); break;
    case 'F' :      FR_1(); break;
    case 'G' :      GR_1(); break;
    case 'a' :      AR_2(); break;
    case 'b' :      BR_2(); break;
    case 'c' :      CR_2(); break;
    case 'd' :      DR_2(); break;
    case 'e' :      ER_2(); break;
    case 'f' :      FR_2(); break;
    case 'g' :      GR_2(); break;
    //case 'X' :      X_call(); break;

  }
  iPianoR++; // for next note.
}

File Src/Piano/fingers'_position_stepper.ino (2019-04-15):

// if the stepper has to move first we have to assure that all the keys are up otherwise we will be having mechanical error.
void up_keysR() {

  digitalWrite(solenoidPin6, LOW);
  digitalWrite(solenoidPin7, LOW);
  digitalWrite(solenoidPin8, LOW);
  digitalWrite(solenoidPin9, LOW);
  digitalWrite(solenoidPin10, LOW);
  prevFlag6 = 0;
  prevFlag7 = 0;
  prevFlag8 = 0;
  prevFlag9 = 0;
  prevFlag10 = 0;
  delay(50);
}
// for stepper to go in right position according to the note which has to be played.
void StepperpositionR(int &stepInitR, int stepFinalR)
{
  analogWrite(A0, 200); // Stepper R
  analogWrite(A1, 200);
  
  digitalWrite(A2, LOW); // Stepper R
  digitalWrite(A3, LOW);
  int x = stepFinalR;
  stepperR.step(stepPerKeyR * (stepInitR - x));
  analogWrite(A0, 0); // Stepper R
  analogWrite(A1, 0);
  digitalWrite(A3, LOW);
  digitalWrite(A2, LOW);
  stepInitR = x;

}

// now if previous flag was 0 and current is 1 , the has to be pressed .
// and if we have to press the same key again that is done too.
void newNoteR() {

  if (prevFlag6 == currFlag6 && currFlag6 == 1)        {
    digitalWrite(solenoidPin6, LOW);
    prevFlag6 = 0;
    delay(30);
  }

  if (prevFlag7 == currFlag7 && currFlag7 == 1)         {
    digitalWrite(solenoidPin7, LOW);
    prevFlag7 = 0;
    delay(30);
  }

  if (prevFlag8 == currFlag8 && currFlag8 == 1)         {
    digitalWrite(solenoidPin8, LOW);
    prevFlag8 = 0;
    delay(30);
  }

  if (prevFlag9 == currFlag9 && currFlag9 == 1)         {
    digitalWrite(solenoidPin9, LOW);
    prevFlag9 = 0;
    delay(30);
  }

  if (prevFlag10 == currFlag10 && currFlag10 == 1)       {
    digitalWrite(solenoidPin10, LOW);
    prevFlag10 = 0;
    delay(30);
  }



  if (prevFlag6 > currFlag6)          digitalWrite(solenoidPin6, LOW);
  else if (prevFlag6 < currFlag6)     digitalWrite(solenoidPin6, HIGH);
  if (prevFlag7 > currFlag7)          digitalWrite(solenoidPin7, LOW);
  else if (prevFlag7 < currFlag7)   digitalWrite(solenoidPin7, HIGH);
  if (prevFlag8 > currFlag8)      digitalWrite(solenoidPin8, LOW);
  else if (prevFlag8 < currFlag8)   digitalWrite(solenoidPin8, HIGH);
  if (prevFlag9 > currFlag9)          digitalWrite(solenoidPin9, LOW);
  else if (prevFlag9 < currFlag9)   digitalWrite(solenoidPin9, HIGH);
  if (prevFlag10 > currFlag10)        digitalWrite(solenoidPin10, LOW);
  else if (prevFlag10 < currFlag10)   digitalWrite(solenoidPin10, HIGH);



  prevFlag6 = currFlag6;
  prevFlag7 = currFlag7;
  prevFlag8 = currFlag8;
  prevFlag9 = currFlag9;
  prevFlag10 = currFlag10;
}
